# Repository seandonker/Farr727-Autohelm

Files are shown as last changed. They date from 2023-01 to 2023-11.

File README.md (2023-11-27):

<b>Project Update<br>
   --------------
Because of different factors such as school, work, and living location, our Farr Sailboat will likely not see water for a few years. For this reason, the project has been halted as on-boat testing is needed for any further programming.

# Farr727-Autohelm

Tiller push/pull based autohelm for a sailboat. Project includes C++ code, CAD files, circuit board files, and pictures. 
This design was started in June, 2021 and it is almost complete, just requiring a few more 3D printed parts, the GUI design to be finished,
and final PID tuning on the boat. 

Commercial auto helms are available for boats using a tiller instead of a wheel (wheel or rudder moving auto helms are much more common) but they are expensive
for the quality of product you get. They are often loud, have primitive controls, and require a separate power source on the boat (which our boat does not have).
The goal of this project was to create an autohelm that was fully battery operated, had a better user interface experience, and was very quiet in operation. 

This project features two main design elements; the controller and the tiller arm receiver. The controller's main function is to sense the boat's
heading and send that data to the tiller arm receiver where it will be translated into rudder movement to correct for any deviations in the boat's course. 
The receiver takes the data sent by the controller and uses a PID loop to determine the correct amount of stepper motor rotation which translates into how
far the tiller moves left or right. A simple diagram of the system can be seen below.  


<b>CONTROLLER<br>
   ----------
The controller unit features a relatively powerful arm microcontroller (Teensy 4.0) that runs a 9-axis IMU heading routine. The teensy also communicates with the bluetooth radio (nrf2401+) in order to send the error in the heading, PID values, and tilt angle of the boat to the receiver. The controller also features four momentary buttons for user input along with an e-paper display and a real time clock as the pesky lift bridge in port stanley only opens every 30 minutes! It uses a wireless charging coil for charging in order to keep it as water tight as possible and the two internal 18650 batteries should last 8+ hours.
<p float="left">
  
   
   
   
   
</p>

<b>TILLER ARM RECEIVER<br>
   -------------------
The tiller arm receiver has a more power efficient and slower microcontroller (Teensy LC) as its main function is to receive the PID data, run the PID loop, and create the desired pulses for the stepper motor driver and none of those routines require much processing. The trinamic 2209 stepper motor driver was used because of its patented quiet step function so the motor operates almost silently. To power the unit, 12 18650 batteries were used in a 6s2p configuration to provide a maximum of 25.2 volts for the motor driver. This high voltage allows the motor to spin faster as the high voltage overcomes the back EMF reducing the risk of stalling and stuttering. The microcontroller monitors the voltage of the battery pack through a voltage divider and periodically sends back the value to be displayed on the control unit. 
<p float="left">
  
  
  
  
  
</p>
  
<b>FINISHING TOUCHES<br>
   -----------------
Before the system can be tested, the GUI has to be roughly completed in order to change PID values on the fly. As for 3D printed parts, a mounting bracket where the controller can slide into needs to be designed. After testing the system and tuning of the motor current on the motor driver, a cover for the tiller arm will be designed and printed as well. The final step will likely be making the GUI look more professional with graphics and better element alignment.

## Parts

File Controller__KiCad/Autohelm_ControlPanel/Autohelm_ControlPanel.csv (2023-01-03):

Source: | C:\Users\seand\Documents\KiCad\Projects\Autohelm_Thruster\Autohelm_ControlPanel\Autohelm_ControlPanel.kicad_sch
Date: | 2022-07-08 12:15:36 AM
Tool: | Eeschema (6.0.6)
Generator: | C:\Program Files\KiCad\6.0\bin\scripting\plugins/bom_csv_grouped_by_value_with_fp.py
Component Count: | 30
Ref | Qnty | Value | Cmp name | Footprint | Description | Vendor
C1, C2, | 2 | 220uF | C | Capacitor_THT:CP_Radial_D5.0mm_P2.00mm | Unpolarized capacitor
C3, C4, C5, C6, C7, C8, | 6 | 6.8uF | C | Capacitor_SMD:C_1812_4532Metric | Unpolarized capacitor
C9, C10, C11, C12, | 4 | 0.1uF | C | Capacitor_SMD:C_1812_4532Metric | Unpolarized capacitor
J1, | 1 | Screw_Terminal_01x04 | Screw_Terminal_01x04 | TerminalBlock:TerminalBlock_bornier-4_P5.08mm | Generic screw terminal, single row, 01x04, script generated (kicad-library-utils/schlib/autogen/connector/)
Q1, | 1 | 2N7002-7-F | 2N7002-7-F | digikey-footprints:SOT-23-3 | MOSFET N-CH 60V 115MA SOT23-3
R1, | 1 | 6.8K | R | Resistor_SMD:R_0805_2012Metric | Resistor
R2, R3, R4, R5, R6, | 5 | 10K | R | Resistor_SMD:R_0805_2012Metric | Resistor
R7, | 1 | 1K | R | Resistor_SMD:R_0805_2012Metric | Resistor
SW1, SW2, SW3, SW4, | 4 | SW_Push | SW_Push | TerminalBlock:TerminalBlock_bornier-2_P5.08mm | Push button switch, generic, two pins
U1, | 1 | NRF24L01_Breakout | NRF24L01_Breakout | RF_Module:nRF24L01_Breakout | Ultra low power 2.4GHz RF Transceiver, Carrier PCB
U2, | 1 | MiniIMU-9_V5 | MiniIMU-9_V5 | Connector_PinHeader_2.54mm:PinHeader_1x04_P2.54mm_Vertical
U3, | 1 | RTC_DS3231M_breakout | RTC_DS3231M_breakout | Connector_PinHeader_2.54mm:PinHeader_1x04_P2.54mm_Vertical
U4, | 1 | Teensy4.0 | Teensy4.0 | teensy:Teensy40
U5, | 1 | e-Paper_Waveshare | e-Paper_Waveshare | Connector_PinHeader_2.54mm:PinHeader_1x08_P2.54mm_Vertical

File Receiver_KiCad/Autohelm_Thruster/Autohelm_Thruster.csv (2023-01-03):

Source: | C:\Users\seand\Documents\KiCad\Projects\Autohelm_Thruster\Autohelm_Thruster.kicad_sch
Date: | 2022-07-08 12:13:04 AM
Tool: | Eeschema (6.0.6)
Generator: | C:\Program Files\KiCad\6.0\bin\scripting\plugins/bom_csv_grouped_by_value_with_fp.py
Component Count: | 12
Ref | Qnty | Value | Cmp name | Footprint | Description | Vendor
Battery_In1, | 1 | Screw_Terminal_01x02 | Screw_Terminal_01x02 | TerminalBlock:TerminalBlock_bornier-2_P5.08mm | Generic screw terminal, single row, 01x02, script generated (kicad-library-utils/schlib/autogen/connector/)
C1, C2, C4, | 3 | 10uF | C | Capacitor_SMD:C_1812_4532Metric | Unpolarized capacitor
C3, | 1 | 220uF | C | Capacitor_THT:CP_Radial_D10.0mm_P5.00mm | Unpolarized capacitor
Motor_Output1, | 1 | Screw_Terminal_01x04 | Screw_Terminal_01x04 | TerminalBlock:TerminalBlock_bornier-4_P5.08mm | Generic screw terminal, single row, 01x04, script generated (kicad-library-utils/schlib/autogen/connector/)
R1, R2, | 2 | 6.8K | R | Resistor_SMD:R_0805_2012Metric | Resistor
U1, | 1 | Mini_Buck_Regulator | Mini_Buck_Regulator | DONKER_footprint_lib:Mini_360_Buck_Convertor_SMD
U2, | 1 | NRF24L01_Breakout | NRF24L01_Breakout | RF_Module:nRF24L01_Breakout | Ultra low power 2.4GHz RF Transceiver, Carrier PCB
U3, | 1 | Teensy-LC | Teensy-LC | teensy:Teensy_LC
U4, | 1 | V3_FYSETC_2209 | V3_FYSETC_2209 | DONKER_footprint_lib:TMC2209_breakout

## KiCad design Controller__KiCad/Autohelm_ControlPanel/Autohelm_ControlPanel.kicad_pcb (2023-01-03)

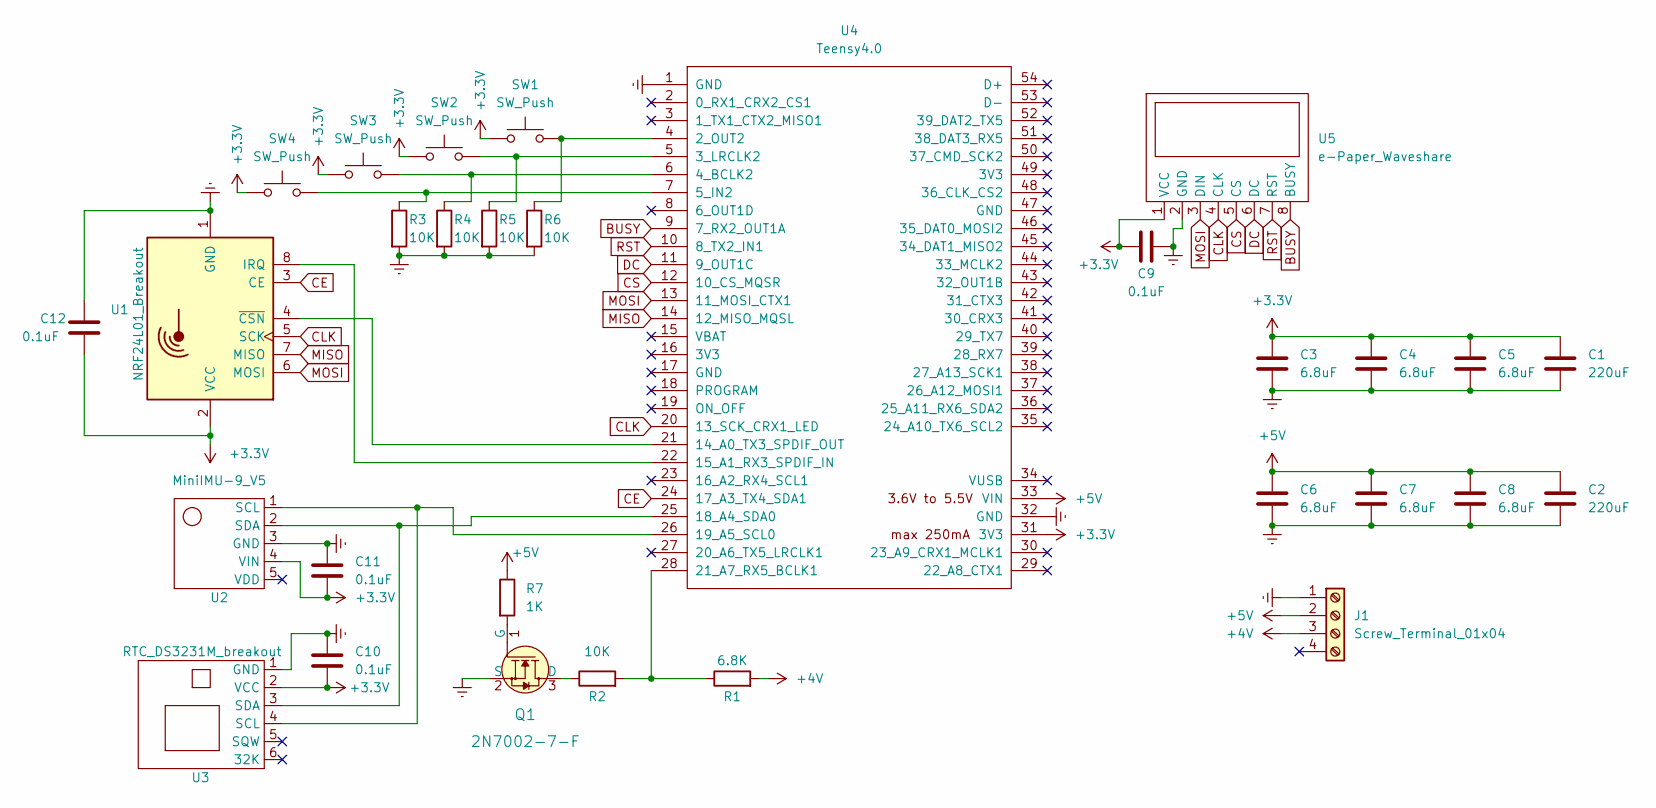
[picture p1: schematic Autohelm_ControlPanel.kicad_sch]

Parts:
C1, C2: 220uF; CP_Radial_D5.0mm_P2.00mm
C3, C4, C5, C6, C7, C8: 6.8uF; C_1812_4532Metric
C9, C10, C11, C12: 0.1uF; C_1812_4532Metric
J1: Screw_Terminal_01x04; TerminalBlock_bornier-4_P5.08mm
Q1: 2N7002-7-F; SOT-23-3; MPN 2N7002-7-F; Digi-Key_PN 2N7002-FDICT-ND
R1: 6.8K; R_0805_2012Metric
R2, R3, R4, R5, R6: 10K; R_0805_2012Metric
R7: 1K; R_0805_2012Metric
SW1, SW2, SW3, SW4: SW_Push; TerminalBlock_bornier-2_P5.08mm
U1: NRF24L01_Breakout; nRF24L01_Breakout
U2: MiniIMU-9_V5; PinHeader_1x04_P2.54mm_Vertical
U3: RTC_DS3231M_breakout; PinHeader_1x04_P2.54mm_Vertical
U4: Teensy4.0; Teensy40
U5: e-Paper_Waveshare; PinHeader_1x08_P2.54mm_Vertical

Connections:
+3.3V: C1.1, C3.1, C4.1, C5.1, C9.2, C10.2, C11.2, C12.2, SW1.1, SW2.1, SW3.1, SW4.1, U1.2 (VCC), U2.4 (VIN), U3.2 (VCC), U4.31 (3V3), U5.1 (VCC)
+4V: J1.3, R1.2
+5V: C2.1, C6.1, C7.1, C8.1, J1.2, R7.1, U4.33 (VIN)
BUSY: U4.9 (7_RX2_OUT1A), U5.8 (BUSY)
CE: U1.3 (CE), U4.24 (17_A3_TX4_SDA1)
CLK: U1.5 (SCK), U4.20 (13_SCK_CRX1_LED), U5.4 (CLK)
CS: U4.12 (10_CS_MQSR), U5.5 (CS)
DC: U4.11 (9_OUT1C), U5.6 (DC)
Earth: C1.2, C2.2, C3.2, C4.2, C5.2, C6.2, C7.2, C8.2, C9.1, C10.1, C11.1, C12.1, J1.1, Q1.2 (S), R3.2, R4.2, R5.2, R6.2, U1.1 (GND), U2.3 (GND), U3.1 (GND), U4.1 (GND), U4.32 (GND), U5.2 (GND)
MISO: U1.7 (MISO), U4.14 (12_MISO_MQSL)
MOSI: U1.6 (MOSI), U4.13 (11_MOSI_CTX1), U5.3 (DIN)
unnamed: Q1.1 (G), R7.2
unnamed: Q1.3 (D), R2.1
unnamed: R1.1, R2.2, U4.28 (21_A7_RX5_BCLK1)
unnamed: R3.1, SW4.2, U4.7 (5_IN2)
unnamed: R4.1, SW3.2, U4.6 (4_BCLK2)
unnamed: R5.1, SW2.2, U4.5 (3_LRCLK2)
unnamed: R6.1, SW1.2, U4.4 (2_OUT2)
unnamed: U1.4 (~CSN), U4.21 (14_A0_TX3_SPDIF_OUT)
unnamed: U1.8 (IRQ), U4.22 (15_A1_RX3_SPDIF_IN)
unnamed: U2.1 (SCL), U3.4 (SCL), U4.26 (19_A5_SCL0)
unnamed: U2.2 (SDA), U3.3 (SDA), U4.25 (18_A4_SDA0)
RST: U4.10 (8_TX2_IN1), U5.7 (RST)

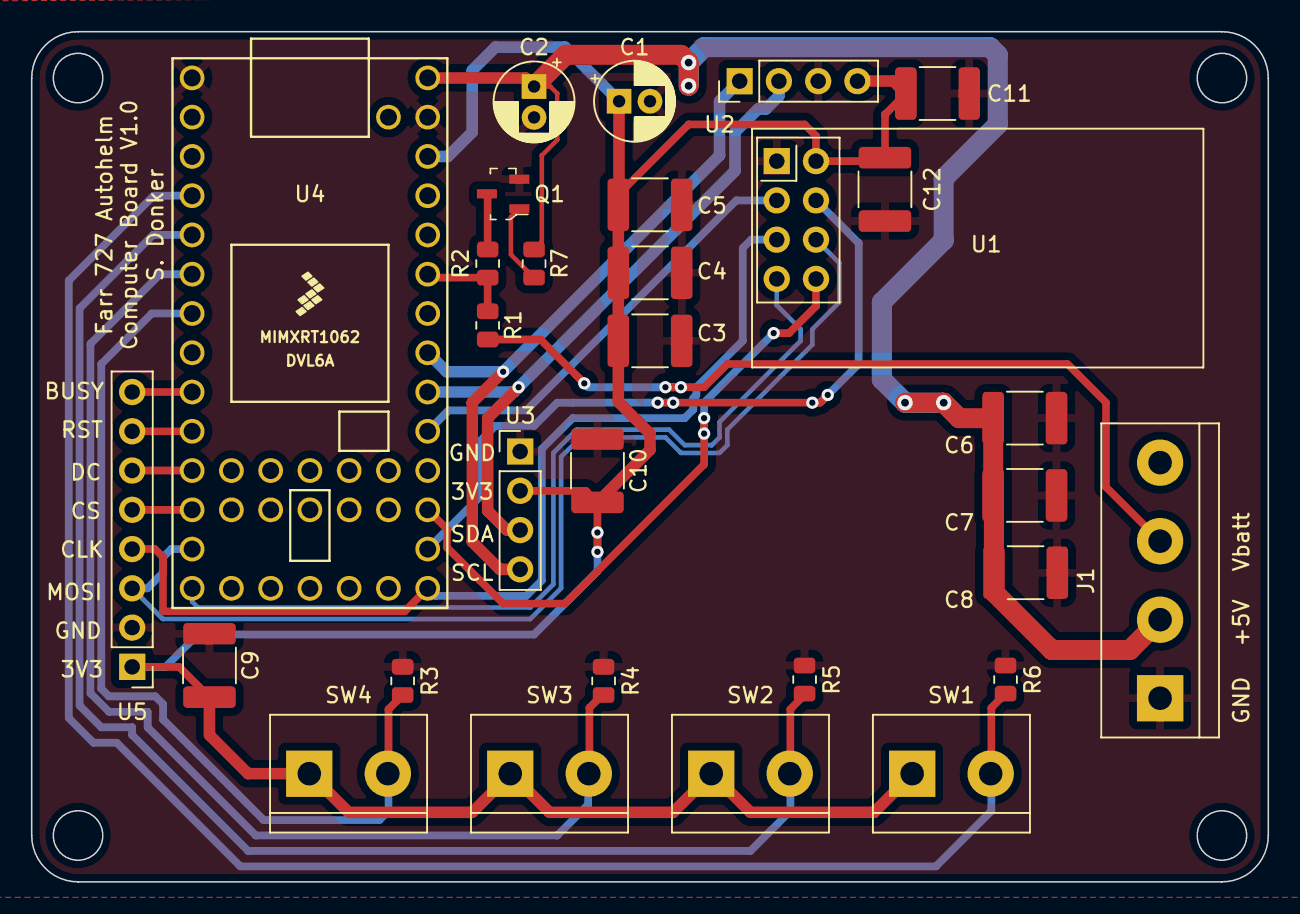
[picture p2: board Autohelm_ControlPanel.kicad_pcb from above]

Board: 2 copper layers, 80.0 x 55.0 mm, 30 parts (0 on the bottom side), 23 nets.

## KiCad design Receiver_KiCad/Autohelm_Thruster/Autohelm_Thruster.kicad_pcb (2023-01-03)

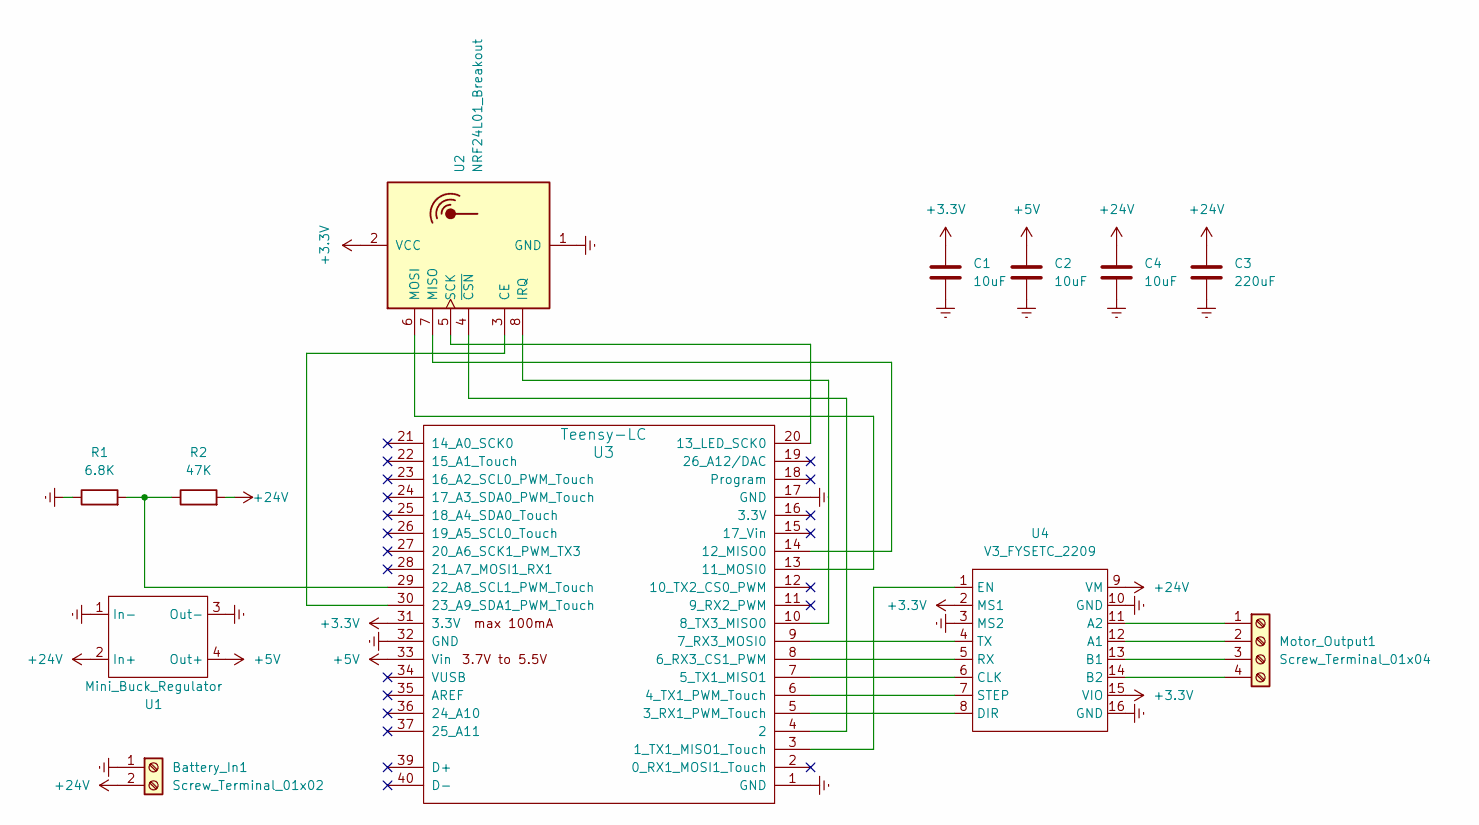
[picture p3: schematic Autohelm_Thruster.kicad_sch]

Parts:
Battery_In1: Screw_Terminal_01x02; TerminalBlock_bornier-2_P5.08mm
C1, C2, C4: 10uF; C_1812_4532Metric
C3: 220uF; CP_Radial_D10.0mm_P5.00mm
Motor_Output1: Screw_Terminal_01x04; TerminalBlock_bornier-4_P5.08mm
R1: 6.8K; R_0805_2012Metric
R2: 47K; R_0805_2012Metric
U1: Mini_Buck_Regulator; Mini_360_Buck_Convertor_SMD
U2: NRF24L01_Breakout; nRF24L01_Breakout
U3: Teensy-LC; Teensy_LC
U4: V3_FYSETC_2209; TMC2209_breakout

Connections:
+3.3V: C1.1, U2.2 (VCC), U3.31 (3.3V), U4.2 (MS1), U4.15 (VIO)
+5V: C2.1, U1.4 (Out+), U3.33 (Vin)
+24V: Battery_In1.2, C3.1, C4.1, R2.2, U1.2 (In+), U4.9 (VM)
Earth: Battery_In1.1, C1.2, C2.2, C3.2, C4.2, R1.1, U1.1 (In-), U1.3 (Out-), U2.1 (GND), U3.1 (GND), U3.17 (GND), U3.32 (GND), U4.3 (MS2), U4.10 (GND), U4.16 (GND)
unnamed 4: Motor_Output1.1, U4.11 (A2); also elsewhere on the board
unnamed 5: Motor_Output1.2, U4.12 (A1); also elsewhere on the board
unnamed 6: Motor_Output1.3, U4.13 (B1); also elsewhere on the board
unnamed 7: Motor_Output1.4, U4.14 (B2); also elsewhere on the board
unnamed: R1.2, R2.1, U3.29 (22_A8_SCL1_PWM_Touch)
unnamed: U2.3 (CE), U3.30 (23_A9_SDA1_PWM_Touch)
unnamed: U2.4 (~CSN), U3.4 (2)
unnamed: U2.5 (SCK), U3.20 (13_LED_SCK0)
unnamed: U2.6 (MOSI), U3.13 (11_MOSI0)
unnamed: U2.7 (MISO), U3.14 (12_MISO0)
unnamed: U2.8 (IRQ), U3.10 (8_TX3_MISO0)
unnamed: U3.3 (1_TX1_MISO1_Touch), U4.1 (EN)
unnamed: U3.5 (3_RX1_PWM_Touch), U4.8 (DIR)
unnamed: U3.6 (4_TX1_PWM_Touch), U4.7 (STEP)
unnamed: U3.7 (5_TX1_MISO1), U4.6 (CLK)
unnamed: U3.8 (6_RX3_CS1_PWM), U4.5 (RX)
unnamed: U3.9 (7_RX3_MOSI0), U4.4 (TX)

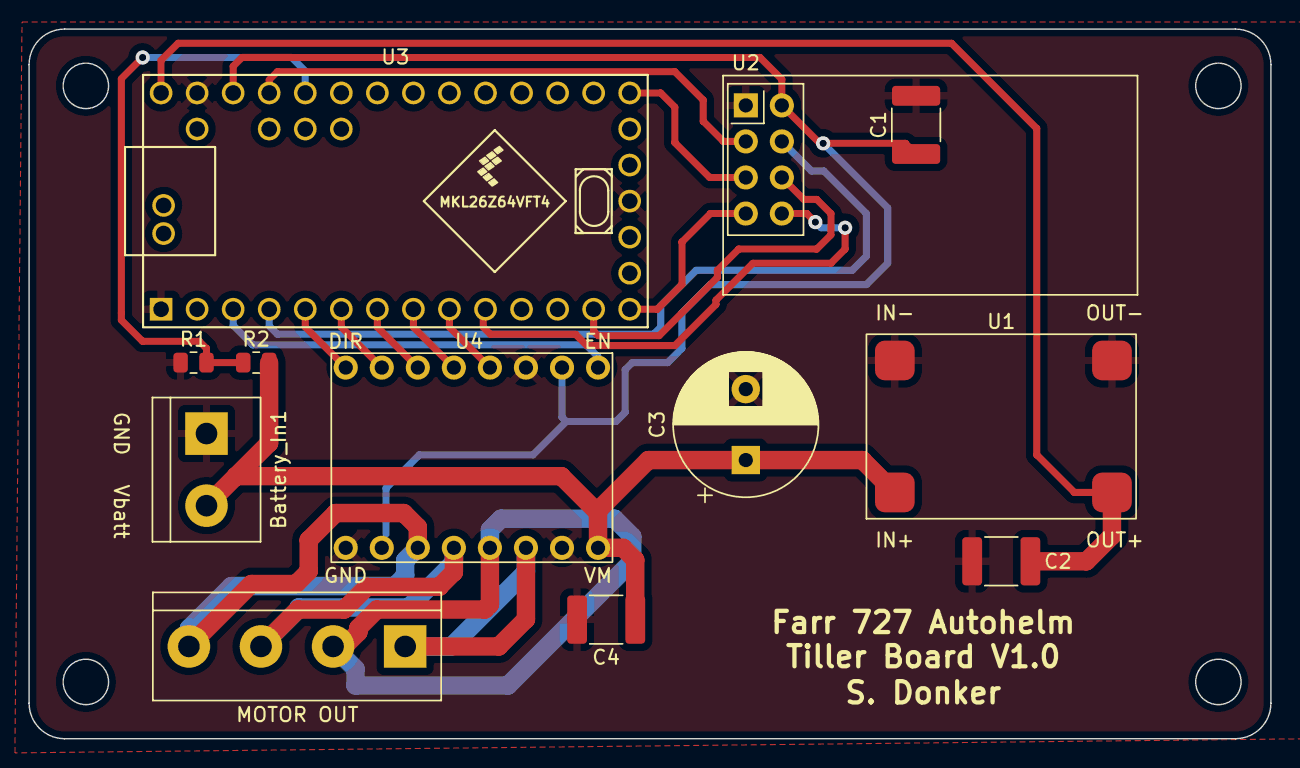
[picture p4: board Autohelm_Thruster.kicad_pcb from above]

Board: 2 copper layers, 87.5 x 50.0 mm, 12 parts (0 on the bottom side), 21 nets.

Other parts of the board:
MOTOR OUT: Screw_Terminal_01x04; TerminalBlock_bornier-4_P5.08mm

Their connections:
unnamed 4: MOTOR OUT.1; also elsewhere on the board
unnamed 5: MOTOR OUT.2; also elsewhere on the board
unnamed 6: MOTOR OUT.3; also elsewhere on the board
unnamed 7: MOTOR OUT.4; also elsewhere on the board

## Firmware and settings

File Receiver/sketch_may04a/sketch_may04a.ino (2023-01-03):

#include "SPI.h"
#include "NRFLite.h"
#include <AccelStepper.h>
#define DIR_PIN 3
#define STEP_PIN 4
#define EN_PIN 1

const static uint8_t RADIO_ID = 0;       // Our radio's id.  The transmitter will send to this id.
const static uint8_t DESTINATION_RADIO_ID = 1; // Id of the radio we will transmit to.
const static uint8_t PIN_RADIO_CE = 23;
const static uint8_t PIN_RADIO_CSN = 2;
//const static uint8_t PIN_LIMIT_SWITCH = 20;
const int analogPin = A8;
//volatile int limitSwitch = 0;
int prevError = 0;
int PID_Output = 0;
int P, I, D = 0;
int stepperSpeed = 0;
int extensionLength = 288000; //360 mm, 2mm pitch, 360/2 * 1600

int sensorValue = 0;        // value read from the pot
int outputValue = 0;        // value output to the PWM (analog out)
long timer;
long timer2;
int timerPID;

struct RadioPacket_Controller{ //sending 10 bytes
  short errorHeading; // 2 bytes, 0-65,535
  unsigned short Proportional;
  unsigned short Integral;
  unsigned short Derivative;
  //unsigned short Heel;     //tilt of boat
};

struct RadioPacket_Receiver{ //sending 2 bytes
  unsigned char BatteryVoltage; 
};

NRFLite radio;
RadioPacket_Receiver radioData_Receiver;
RadioPacket_Controller radioData_Controller;

AccelStepper stepper(AccelStepper::DRIVER, STEP_PIN, DIR_PIN, true); 

void setup()
{  
  Serial.begin(115200);
  if (!radio.init(RADIO_ID, PIN_RADIO_CE, PIN_RADIO_CSN, NRFLite::BITRATE2MBPS, 100)){
    Serial.println("Cannot communicate with radio");
    while (1); // Wait here forever.
  }
  radioData_Controller.errorHeading = 0;
  
  pinMode(1, OUTPUT);
  //attachInterrupt(digitalPinToInterrupt(PIN_LIMIT_SWITCH), interrupt_LimitSwitch, RISING);
  digitalWrite(1,LOW);
  
  stepper.setMaxSpeed(5000); //8000 maxish
  stepper.setAcceleration(8000); //5000
  stepper.setCurrentPosition(0);
  //homeStepper();
  timer = millis();
  timer2 = millis();
  //timer3 = millis(); //saftey stop
  //Serial.println(stepper.targetPosition());
}

void loop()
{
    if(stepperSpeed == 0 && ((millis() - timer) > 10000)){      //every 10 seconds, send 
      sensorValue = analogRead(analogPin);
      outputValue = map(sensorValue, 0, 1023, 0, 262); //increase of reading low
      radioData_Receiver.BatteryVoltage = outputValue - 69; //scaleFactor, so less than 255
      radio.send(DESTINATION_RADIO_ID, &radioData_Receiver, sizeof(radioData_Receiver));
      Serial.println("SENDING BLUETOOTH");
      Serial.println(radioData_Receiver.BatteryVoltage);
      timer = millis();
    }
    stepper.runSpeed();
    
    if (radio.hasData()) //uses while for some reason?
    {
        prevError = radioData_Controller.errorHeading;
        radio.readData(&radioData_Controller);
        timerPID = millis() - timer2;
        
//        P = radioData_Controller.Proportional * radioData_Controller.errorHeading;
//        I += radioData_Controller.Integral * (radioData_Controller.errorHeading * timerPID);
//        D = radioData_Controller.Derivative * (radioData_Controller.errorHeading - prevError)/timerPID;
//        PID_Output = P + I + D;
//        timer2 = millis();

        P = 1000 * radioData_Controller.errorHeading/5; //1-500 ish
        //I += 0 * (radioData_Controller.errorHeading * timerPID) / 2000; //1-500 ish
        I = 0;
        D = 0 * ((double)(radioData_Controller.errorHeading - prevError)* 1500)/(double)(timerPID); //1-500 ish
        PID_Output = P + I + D;
        timer2 = millis();
        stepperSpeed = -PID_Output/10; //8000 maxish
        stepper.setSpeed(stepperSpeed);
        //if(radioData_Controller.errorHeading > 0)
        //  stepper.move(-800*10); //800 for 1 rot (1/4)
        //else
        //  stepper.move(800*10); //800 for 1 rot  (1/4)
        String msg = "ERROR :";
        msg += radioData_Controller.errorHeading;
        msg += ", P: ";
        msg += P;
        msg += " , I:";
        msg += I;
        msg += " , D:";
        msg += D;

        Serial.println(msg);
    }
}

//void interrupt_LimitSwitch(){
//  noInterrupts();
//  if(limitSwitch == 0)
//    limitSwitch = 1;
//  interrupts();
//}

void homeStepper(){
  while(1){
    stepper.runToNewPosition(-50000); //36 cm,move to hit limit switch
    stepper.runToNewPosition(+50000); //36 cm,move to hit limit switch
  }
  stepper.runToNewPosition(-extensionLength-3200); //36 cm,move to hit limit switch
  delay(1000);
  stepper.setCurrentPosition(-1600);  //home position is 0, don't want to repeatedly hit switch
  stepper.moveTo(0); //800 for 1 rot (1/4)
  stepper.runToPosition();
  delay(2000);
  stepper.moveTo(extensionLength/2);  //move out to half extension
  stepper.runToPosition();
}

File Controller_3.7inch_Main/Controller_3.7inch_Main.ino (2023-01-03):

#include <Wire.h>
#include <LSM6.h>
#include <LIS3MDL.h>
#include <SPI.h>
#include <string.h>
#include <cstdlib>
#include <algorithm>
#include <iterator>
#include "epd3in7.h"
#include "imagedata.h"
#include "epdpaint.h"
#include "NRFLite.h"
#include "RTClib.h"

void IMU_Routine(void);
void delayWithIMU(int delayMili);
//*********************************************************DISPLAY
#define COLORED     0
#define UNCOLORED   1
Epd epd;
UBYTE baseBlank_Image[16800];                  //280 x 480 / 8
UBYTE baseHome_Image[16800];
UBYTE holdHome_Image[16800];
UBYTE setHome_Image[16800];
UBYTE menuHome_Image[16800];
UBYTE PIDHome_Image[16800];
Paint baseHome(baseHome_Image, 280, 480);    //base screen without info (should never display this), width should be the multiple of 8 
Paint holdHome(holdHome_Image, 280, 480);    //after startup, not set heading yet
Paint setHome(setHome_Image, 280, 480);     //heading set, home screen
Paint baseBlank(baseBlank_Image, 280, 480);   //blank home
Paint menuHome(menuHome_Image, 280, 480);     //menu home
Paint PIDHome(PIDHome_Image, 280, 480);     //menu home
char headingString[6];

//*********************************************************RADIO
const static uint8_t RADIO_ID = 1;             // Our radio's id.
const static uint8_t DESTINATION_RADIO_ID = 0; // Id of the radio to transmit to.
const static uint8_t PIN_RADIO_CE = 17;  //CHANGE TO 17 for pcb
const static uint8_t PIN_RADIO_CSN = 14;
const int analogPin = A7;

struct RadioPacket_Controller{ //sending 10 bytes, un
  //unsigned short 0 -> 65535, signed short -32768 -> 32767 (both 2 bytes, 16 bits)
  short errorHeading;
  unsigned short Proportional = 5;
  unsigned short Integral = 6;
  unsigned short Derivative = 7;
  short Heel;     //tilt of boat
};
struct RadioPacket_Receiver{ //sending 2 bytes
  unsigned char BatteryVoltage; 
};
//RadioPacket_Receiver.BatteryVoltage = 0;
NRFLite radio;
RadioPacket_Receiver radioData_Receiver;
RadioPacket_Controller radioData_Controller;

//*********************************************************IMU
LSM6 gyro_acc;
LIS3MDL mag;
int SENSOR_SIGN[9] = {1,1,1,-1,-1,-1,1,1,1}; //Correct directions x,y,z - gyro, accelerometer, magnetometer
#define GRAVITY 256  //this equivalent to 1G in the raw data coming from the accelerometer
#define ToRad(x) ((x)*0.01745329252)  // *pi/180
#define ToDeg(x) ((x)*57.2957795131)  // *180/pi
#define Gyro_Gain_X 0.07 //X axis Gyro gain
#define Gyro_Gain_Y 0.07 //Y axis Gyro gain
#define Gyro_Gain_Z 0.07 //Z axis Gyro gain
#define Gyro_Scaled_X(x) ((x)*ToRad(Gyro_Gain_X)) //Return the scaled ADC raw data of the gyro in radians for second
#define Gyro_Scaled_Y(x) ((x)*ToRad(Gyro_Gain_Y)) //Return the scaled ADC raw data of the gyro in radians for second
#define Gyro_Scaled_Z(x) ((x)*ToRad(Gyro_Gain_Z)) //Return the scaled ADC raw data of the gyro in radians for second

#define M_X_MIN -2988   //Calibrate sensor by running calibration and "painting inside of sphere"
#define M_Y_MIN 761
#define M_Z_MIN -9586
#define M_X_MAX 4465
#define M_Y_MAX 7950
#define M_Z_MAX -2324

#define Kp_ROLLPITCH 0.02
#define Ki_ROLLPITCH 0.00002
#define Kp_YAW 1.2
#define Ki_YAW 0.00002
#define STATUS_LED 13

float G_Dt=0.02;    // Integration time (DCM algorithm)  We will run the integration loop at 50Hz if possible

long timer=0;   //general purpuse timer
long timer_old;
long loop_start = 0;
long loop_end = 0;
long timer24=0; //Second timer used to print values
int AN[6]; //array that stores the gyro and accelerometer data
int AN_OFFSET[6]={0,0,0,0,0,0}; //Array that stores the Offset of the sensors

int gyro_x;
int gyro_y;
int gyro_z;
int accel_x;
int accel_y;
int accel_z;
int magnetom_x;
int magnetom_y;
int magnetom_z;
float c_magnetom_x;
float c_magnetom_y;
float c_magnetom_z;
float MAG_Heading;

float Accel_Vector[3]= {0,0,0}; //Store the acceleration in a vector
float Gyro_Vector[3]= {0,0,0};//Store the gyros turn rate in a vector
float Omega_Vector[3]= {0,0,0}; //Corrected Gyro_Vector data
float Omega_P[3]= {0,0,0};//Omega Proportional correction
float Omega_I[3]= {0,0,0};//Omega Integrator
float Omega[3]= {0,0,0};
// Euler angles
float roll;
float pitch;
float yaw;
float errorRollPitch[3]= {0,0,0};
float errorYaw[3]= {0,0,0};
unsigned int counter=0;
byte gyro_sat=0;
float DCM_Matrix[3][3]={{1,0,0},{0,1,0},{0,0,1}};
float Update_Matrix[3][3]={{0,1,2},{3,4,5},{6,7,8}}; //Gyros here
float Temporary_Matrix[3][3]={{0,0,0},{0,0,0},{0,0,0}};

//*********************************************************GENERAL
#define LEFTLEFT_BUT_PIN 5
#define LEFT_BUT_PIN 4
#define RIGHT_BUT_PIN 3
#define RIGHTRIGHT_BUT_PIN 2

volatile int buttonStates[4] = {0, 0, 0, 0}; //White, Red, Green, Yellow. Even is finished button excecution.
static unsigned long last_interrupt = 0;
unsigned long interrupt = 0;
int currentlyActive = 0;   //ZERO FALSE
int setHeading = 0;
short actualHeading=0;
int buttonStateSum;
int sensorValue = 0;        // value read from the pot
int outputValue = 0;        // value output to the PWM (analog out)
double averageOutput[5] = {0,0,0,0,0};
short controlActive = 0; //0 false, 1 true, unit starts by not moving

RTC_DS3231 rtc;

void setup() {
  IMU_Init(); //accel, gyro, and compass
  Peripheral_Init(); //e-paper, rtc, button interrupts, radio
  Epaper_base_designs();

  //epd.Init();
  timer=millis();
  counter=0;
  
  epd.Init();
  epd.DisplayFrame(holdHome.GetImage(), true);
  Serial.println("*****SETUP DONE*****\n\n");
  epd.Sleep();
}

void loop() {
  //IMU_Routine(); //This routine has radio send function as well at 50hz

  buttonStateSum = 0;
  for(int i = 0; i < 4; i++){ //creates sum of button states, (states change from interrupt)
    buttonStateSum += buttonStates[i];
  }
  if(buttonStateSum % 2 != 0) //runs if odd, (button press)
    handleButtonStates();  //ISR change button states, this function displays menu depending on states
  if (radio.hasData()){
    //epd.DisplayFrame(baseBlank.GetImage(), true);
  }
}

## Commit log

2023-01-03 Code for main control unit (Compass, Display, Buttons)
2023-01-03 Code for tiller driver (stepper motor)
2023-01-03 CAD for circuit board (includes GERBER output)
    [Autohelm_Thruster-B_Cu.gbl, Autohelm_Thruster-B_Mask.gbs, Autohelm_Thruster-B_Paste.gbp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]
